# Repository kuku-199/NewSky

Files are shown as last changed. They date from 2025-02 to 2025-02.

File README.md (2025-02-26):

<<<<<<< HEAD
# NewSky📺
          
* [**中文版本**](/README_zh.md)

## Overview📖

=======
<h1 align="center">NewSky</h1>

           
* [**中文版本**](/README_zh.md)

## Overview📖
**Let beginners start making their own aircraft from scratch✈️**<br>
Projects that you can personally create:flight control ，racks (At present, we are not considering the production of ESC (the cost is too high))

**Supports multiple firmware options💿**<br>
NewSky Currently possessingPX4 Betaflight Inav Ardupolit firmware 

**Having different flight control models⚙️**<br>
NewSky use STM32 series as the main controller

## ⚠️⚠️⚠️ Commercial use without permission is strictly prohibited❗❗❗

### 📊Project Status 

|Complete|Making|Not started|
|-|-|-|
|✔|🛠️|❌|

## ⚙️Hardware<br>
### Flight controller
- ***NewSkyF7-Air*** ✔<br>

|Top|Bottom|
|:--:|:--:|
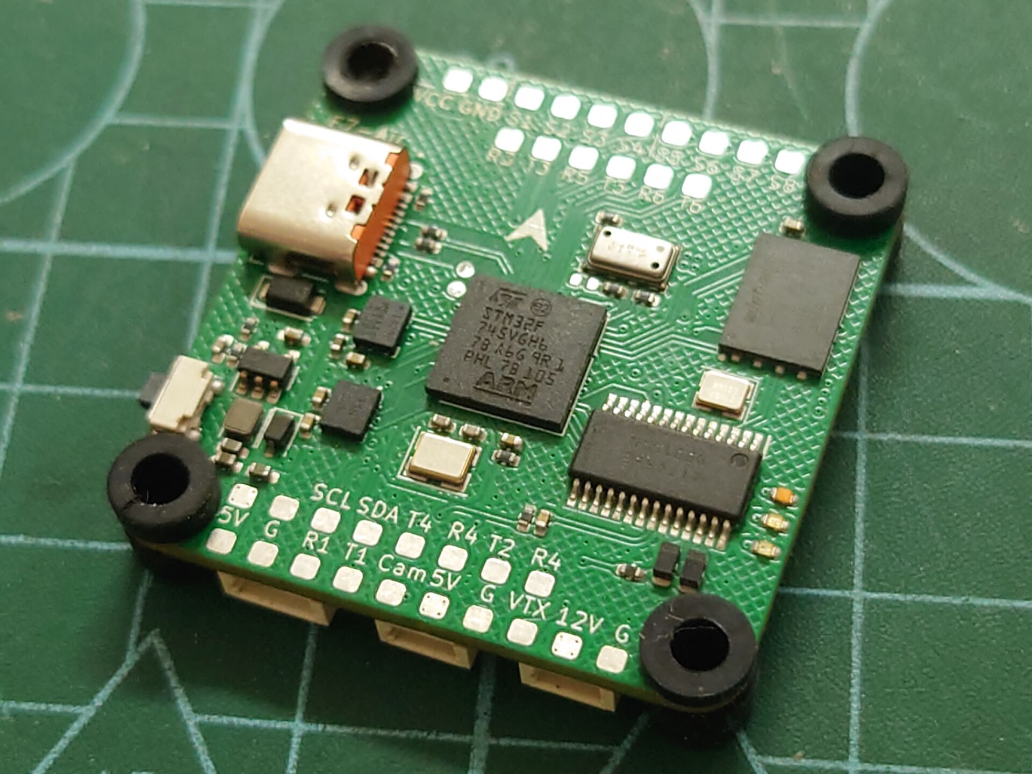
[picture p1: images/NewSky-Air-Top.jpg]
"up"
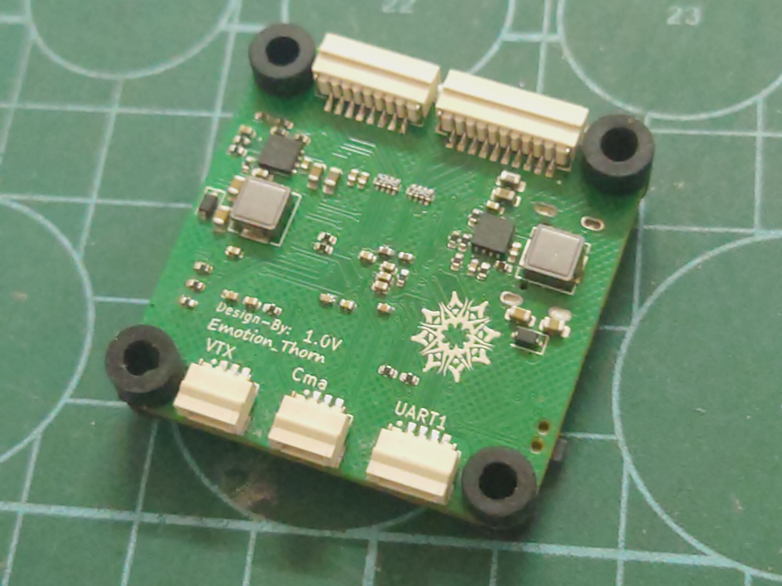
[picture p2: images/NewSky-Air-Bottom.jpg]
"down"
|||

- STM32F745VG(Cortex-M7)
- Have three BEC (Max input 36V)
    - 12V 3A
    - 5V 3A 
    - 3V3 2A
- Have two IMU
    - BMI270
    - IMC4288P
- On-board barometer(MS5611)
- On-board FLASH(W25Q256/W25N01G)
- On-board OSD(AT7456)
> In addition to the provided pad, which can be soldered, the board can use JST-SH

>Due to the lack of DMA channels in S5 S6, it seems that X8 mode (8 motors) cannot be activated on Betaflight at present

> The PCB engineering files have been open-source

- ***H7-Pro*** 🛠️

## ....

## 💿Firmware<br>
- Betaflight
    - NewSkyF7-Air (4.4.4-Beta)
- Ardupolit🛠️
- Inav🛠️
- PX4🛠️

## 🌐Wireless connection ground station 🛠️<br>
>>>>>>> c5ff180fc82f0e98c3e5e9217bb21fad2d1e034f

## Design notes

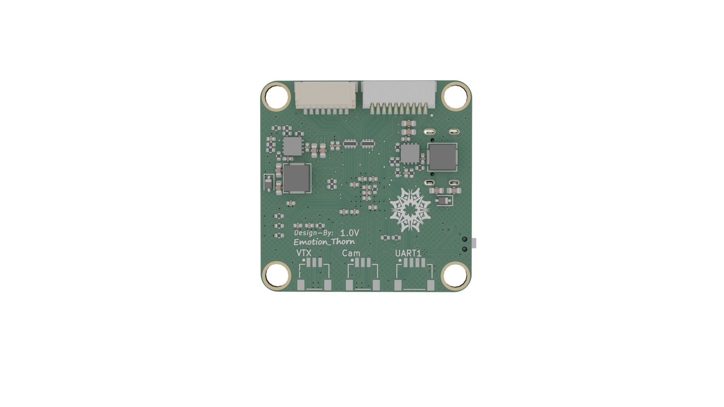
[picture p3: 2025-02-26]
images/NewSky-Air-Bottom1.png

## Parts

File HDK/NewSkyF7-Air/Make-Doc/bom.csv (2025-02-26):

Designator | Footprint | Quantity | Value | LCSC Part #
C1, C2, C3, C4 | 0603 | 4 | 10uF
C10, C11, C22, C24, C25, C27, C29, C30, C31, C32, C33, C36, C37, C38, C40, C41, C42, C44, C46, C5, C6, C8, C9 | 0402 | 23 | 100nF
C12 | 0402 | 1 | 6.8pF
C13, C16, C19 | 0402 | 3 | 10uF
C14, C15, C17, C18 | 0603 | 4 | 22uF
C20, C21 | 0402 | 2 | 15pF
C23, C7 | 0402 | 2 | 4.7uF
C26, C28, C45 | 0402 | 3 | 2.2uF
C34, C35 | 0603 | 2 | 47uF
C43 | 0402 | 1 | 10nF
D1, D2, D3 | D_SOD-323 | 3 | LESD3Z5.0CMT1G
D4 | 0402 | 1 | Red
D5 | 0402 | 1 | Yellow
D6 | 0402 | 1 | Blue
D7 | D_SOD-123F | 1 | K24
IC1, IC2 | MP9943GQZ | 2 | MP9943GQ-Z
IC3 | IIM42352 | 1 | ICM-42688-P
IC4 | SON127P800X600X80-9N-D | 1 | W25Q256JVEIQ
J1 | JST_SM04B-SRSS-TB(LF)(SN) | 1 | SBUS
J10, J11, J12, J13, J14, J15, J16, J17, J18, J19, J20, J21, J22, J23, J24, J25, J26, J27, J28, J29, J30, J31, J32, J33, J34, J37, J38, J39, J40, J5, J6, J7, J8, J9 | Test | 34 | Conn_01x01_Socket
J2 | JST_SM03B-SRSS-TB(LF)(SN) | 1 | VTX
J3 | JST_SM03B-SRSS-TB(LF)(SN) | 1 | Camera
J35 | NewSkyF7 | 1 | ~
J36 | SM10B-SRSS-TB | 1 | Conn_01x10_Socket
J4 | SH1.0mm_8P | 1 | Input
J41, J42 | TestPoint_Pad_D1.0mm | 2 | Conn_01x01_Socket
L1 | L_Murata_DFE201610P | 1 | 2.2uH
L2, L3 | L_Sunlord_MWSA0402S | 2 | L
R1, R2, R3, R33, R4, R6 | 0402 | 6 | 100K
R10, R24, R25, R8 | 0402 | 4 | 22R
R11 | 0402 | 1 | 3K
R12 | 0402 | 1 | 7.68K
R13, R14 | 0402 | 2 | 41.2K
R15, R18, R19, R29, R30, R34, R35 | 0402 | 7 | 10K
R16, R20, R21, R26 | 0402 | 4 | 1K
R17 | 0402 | 1 | 3.3K
R22, R23 | 0402 | 2 | 5.1K
R27, R28 | 0402 | 2 | 75R
R31, R32 | 0402 | 2 | [N/S]
R5 | 0402 | 1 | 442K
R7, R9 | 0402 | 2 | 51K
RN1, RN2 | R_Array_Concave_4x0402 | 2 | 22R
SW1 | 2x4_side | 1 | BOOT0
U1 | SOT-23-5 | 1 | TLV62569DBV
U2 | TFBGA-100_8x8mm_Layout10x10_P0.8mm | 1 | STM32F745VGH6
U4 | Typc-C-16P | 1 | USB_C_16P
U5 | SOP65P640X120-29N | 1 | AT7456E
U6 | XDCR_BMI270 | 1 | BMI270
U8 | LGA-8_3x5mm_P1.25mm | 1 | MS5611-01BA
Y1 | Crystal_SMD_3225-4Pin_3.2x2.5mm | 1 | 25M
Y2 | Crystal_SMD_2520-4Pin_2.5x2.0mm | 1 | 27M

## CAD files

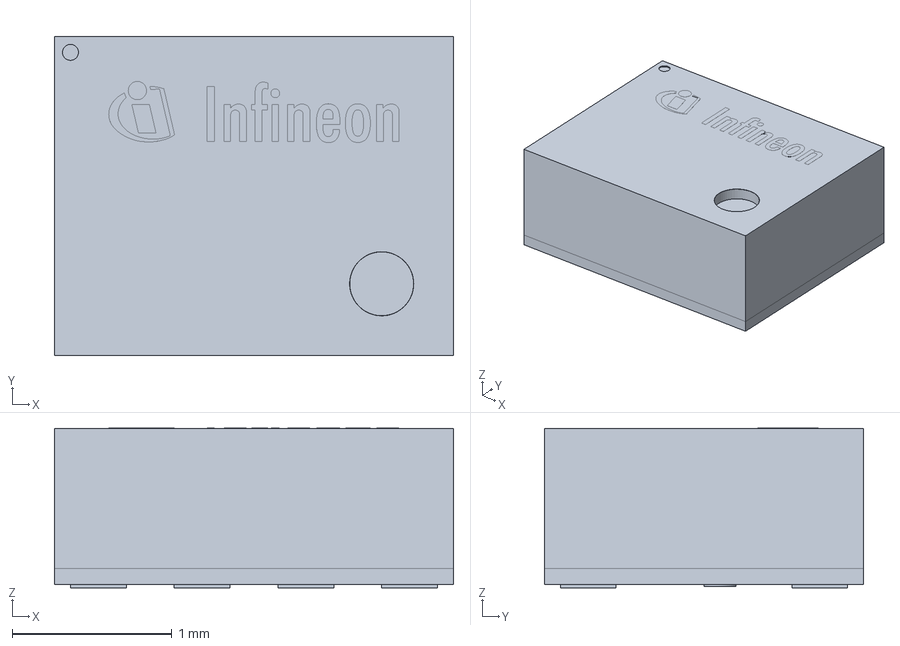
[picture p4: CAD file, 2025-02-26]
HDK/Design-file/3D/DPS310XTSA1.stp
2.50 x 2.00 x 1.00 mm
CADSOFTTOOLS 2.1
CADSOFTTOOLS 2.2
CADSOFTTOOLS 2.3
CADSOFTTOOLS 2.4
CADSOFTTOOLS 2.5
CADSOFTTOOLS 2.6
CADSOFTTOOLS 2.7
CADSOFTTOOLS 2.8
CADSOFTTOOLS 2.9
CADSOFTTOOLS 2.10
CADSOFTTOOLS 2.11
CADSOFTTOOLS 2.12
CADSOFTTOOLS 2.13
CADSOFTTOOLS 2.14
CADSOFTTOOLS 2.15
CADSOFTTOOLS 2.16
CADSOFTTOOLS 2.17
CADSOFTTOOLS 2.18
CADSOFTTOOLS 2.19
CADSOFTTOOLS 2.20
CADSOFTTOOLS 2.21
CADSOFTTOOLS 2.22
CADSOFTTOOLS 2.23
CADSOFTTOOLS 2.24
CADSOFTTOOLS 2.25
CADSOFTTOOLS 2.26
CADSOFTTOOLS 2.27
CADSOFTTOOLS 2.28
CADSOFTTOOLS 2.29
CADSOFTTOOLS 2.30
CADSOFTTOOLS 2.31
CADSOFTTOOLS 2.32
CADSOFTTOOLS 2.33
CADSOFTTOOLS 2.34
CADSOFTTOOLS 2.35
CADSOFTTOOLS 2.36
CADSOFTTOOLS 2.37
CADSOFTTOOLS 2.38
CADSOFTTOOLS 2.39
CADSOFTTOOLS 2.40
CADSOFTTOOLS 2.41
CADSOFTTOOLS 2.42
CADSOFTTOOLS 2.43
CADSOFTTOOLS 2.44
CADSOFTTOOLS 2.45
CADSOFTTOOLS 2.46
CADSOFTTOOLS 2.47
CADSOFTTOOLS 2.48
CADSOFTTOOLS 2.49
CADSOFTTOOLS 2.50
CADSOFTTOOLS 2.51
CADSOFTTOOLS 2.52
CADSOFTTOOLS 2.53
CADSOFTTOOLS 2.54
CADSOFTTOOLS 2.55
CADSOFTTOOLS 2.56
CADSOFTTOOLS 2.57
CADSOFTTOOLS 2.58
CADSOFTTOOLS 2.59
CADSOFTTOOLS 2.60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

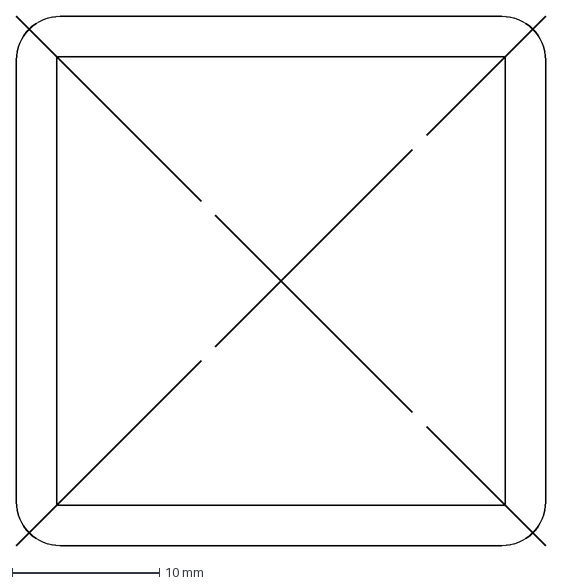
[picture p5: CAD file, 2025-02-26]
HDK/NewSkyF7-Air/Outline.dxf
36.0 x 36.0 mm

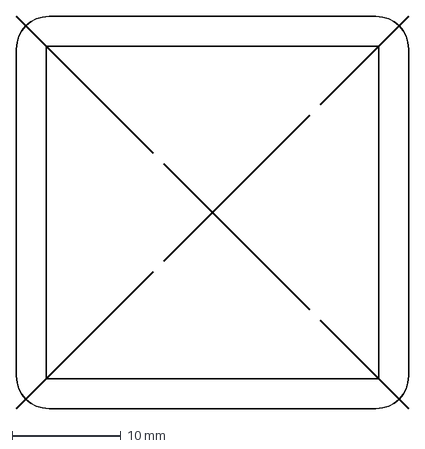
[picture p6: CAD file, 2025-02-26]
HDK/NewSkyH7-Air/Outline.dxf
36.0 x 36.0 mm

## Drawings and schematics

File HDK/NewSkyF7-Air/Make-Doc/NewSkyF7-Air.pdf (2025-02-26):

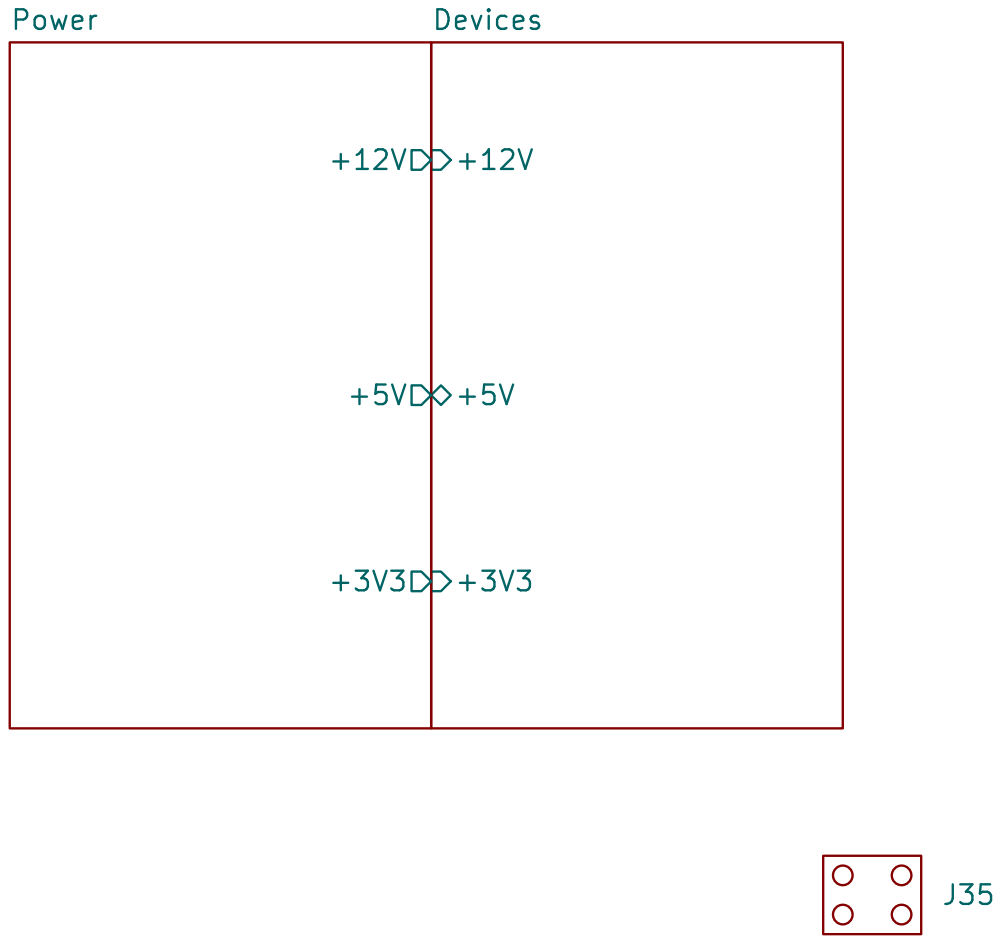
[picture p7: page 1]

Id: 1/7 Title: NewSkyF7-Air File: / Sheet: /

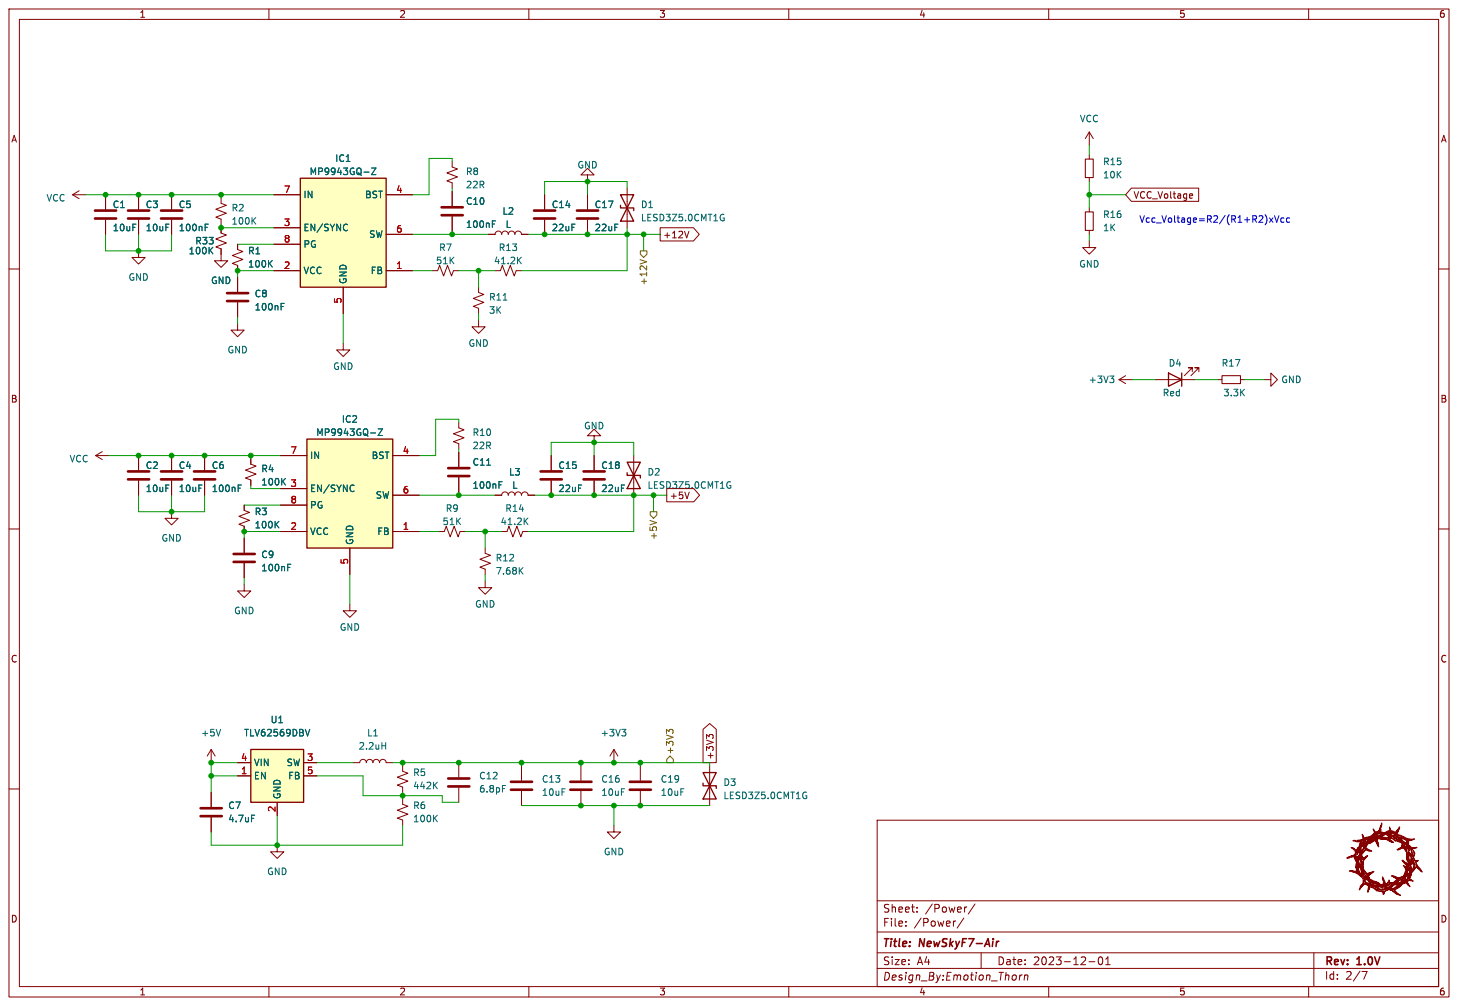
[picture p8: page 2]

Id: 2/7 Title: NewSkyF7-Air File: /Power/ Sheet: /Power/ +3V3

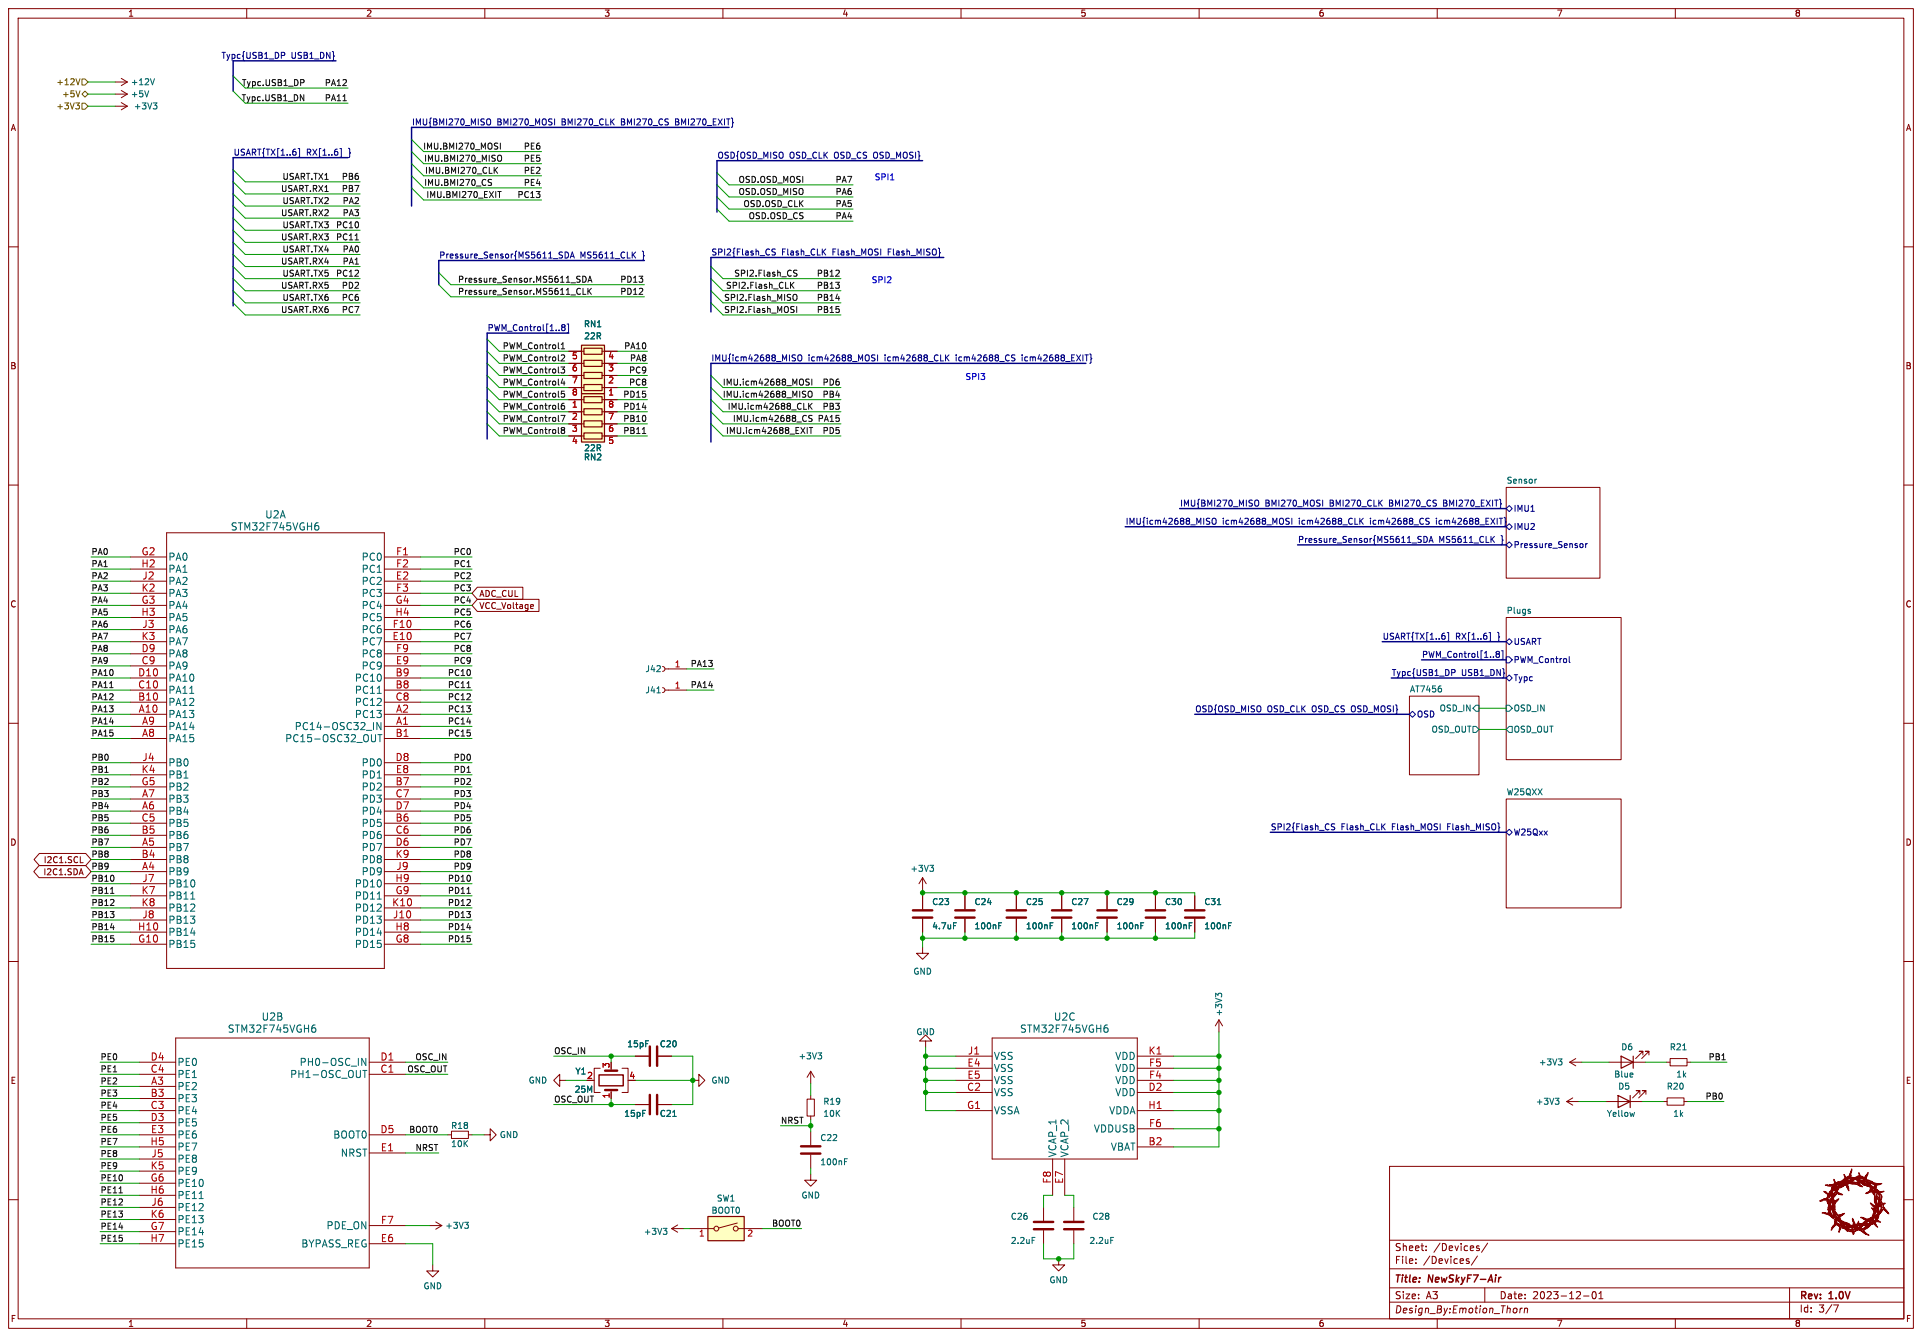
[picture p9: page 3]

Id: 3/7 Title: NewSkyF7-Air File: /Devices/ Sheet: /Devices/

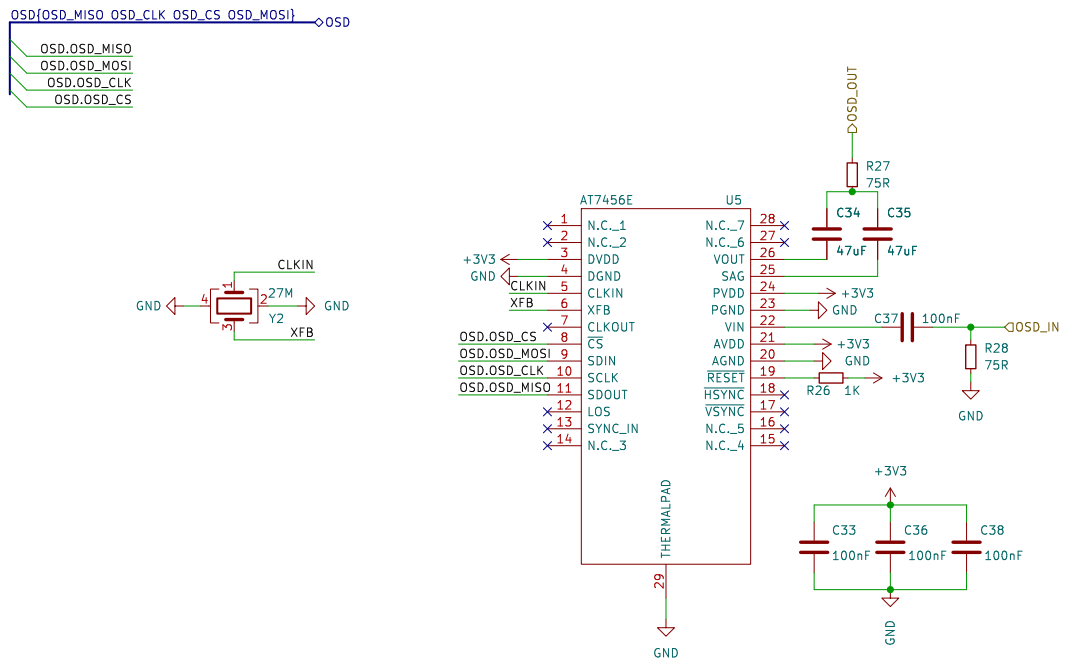
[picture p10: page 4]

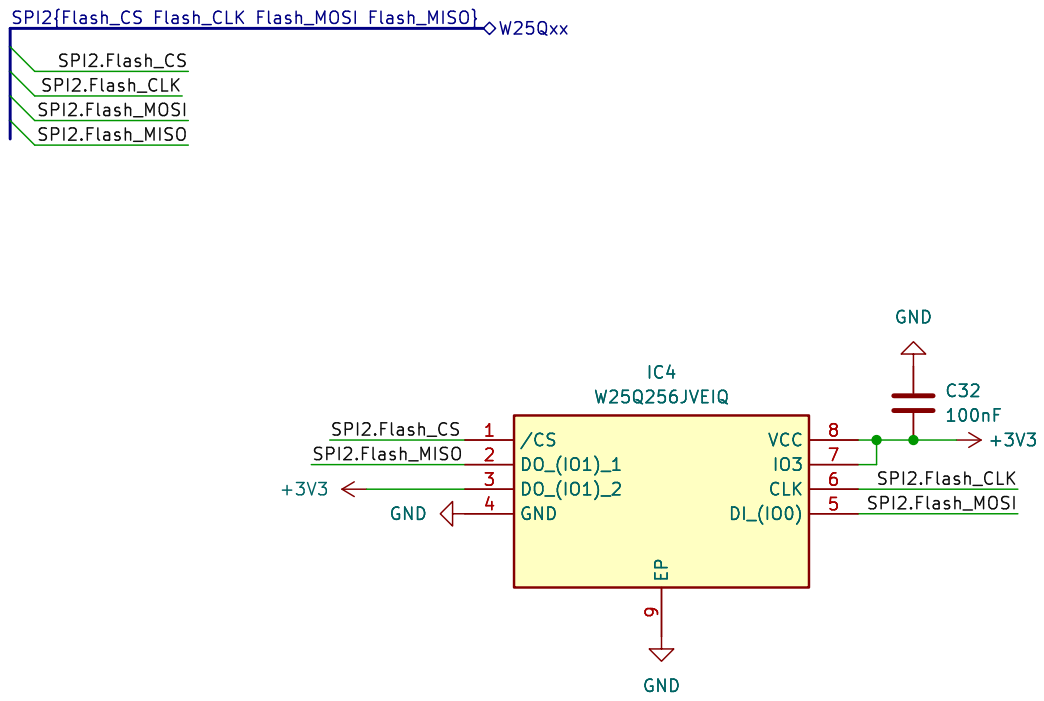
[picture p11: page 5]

Id: 5/7 Title: NewSkyF7-Air File: /Devices/W25QXX/ Sheet: /Devices/W25QXX/

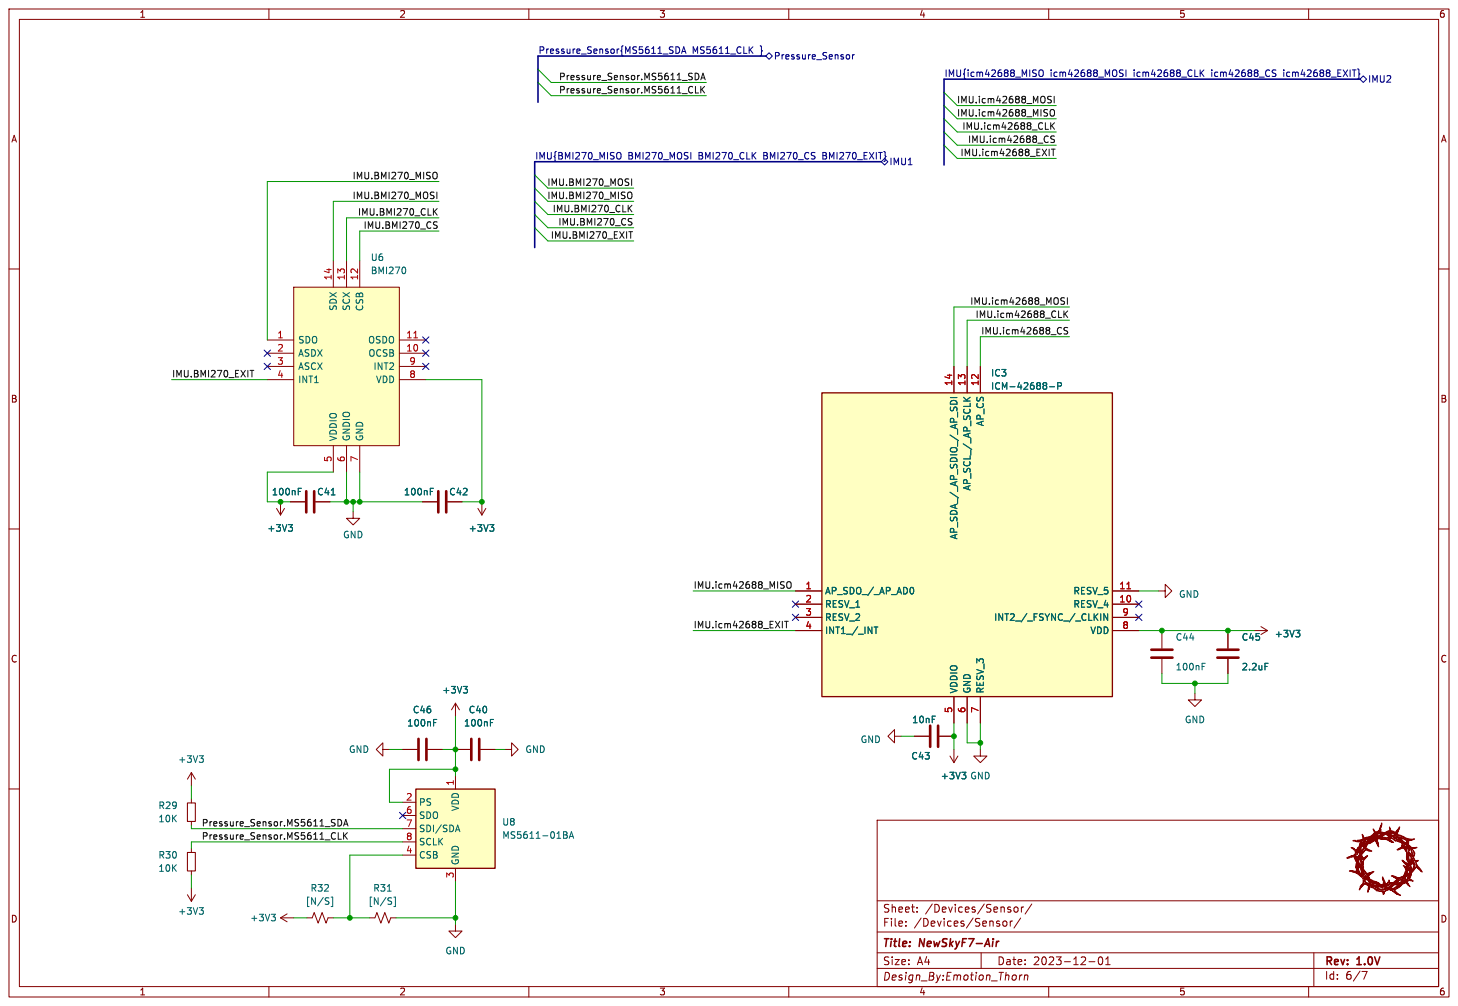
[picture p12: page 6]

3 CSB 4 SDO 6 SDI/SDA 7 SCLK 8 U8 MS5611-01BA GND

Id: 6/7 Title: NewSkyF7-Air File: /Devices/Sensor/ Sheet: /Devices/Sensor/ R32

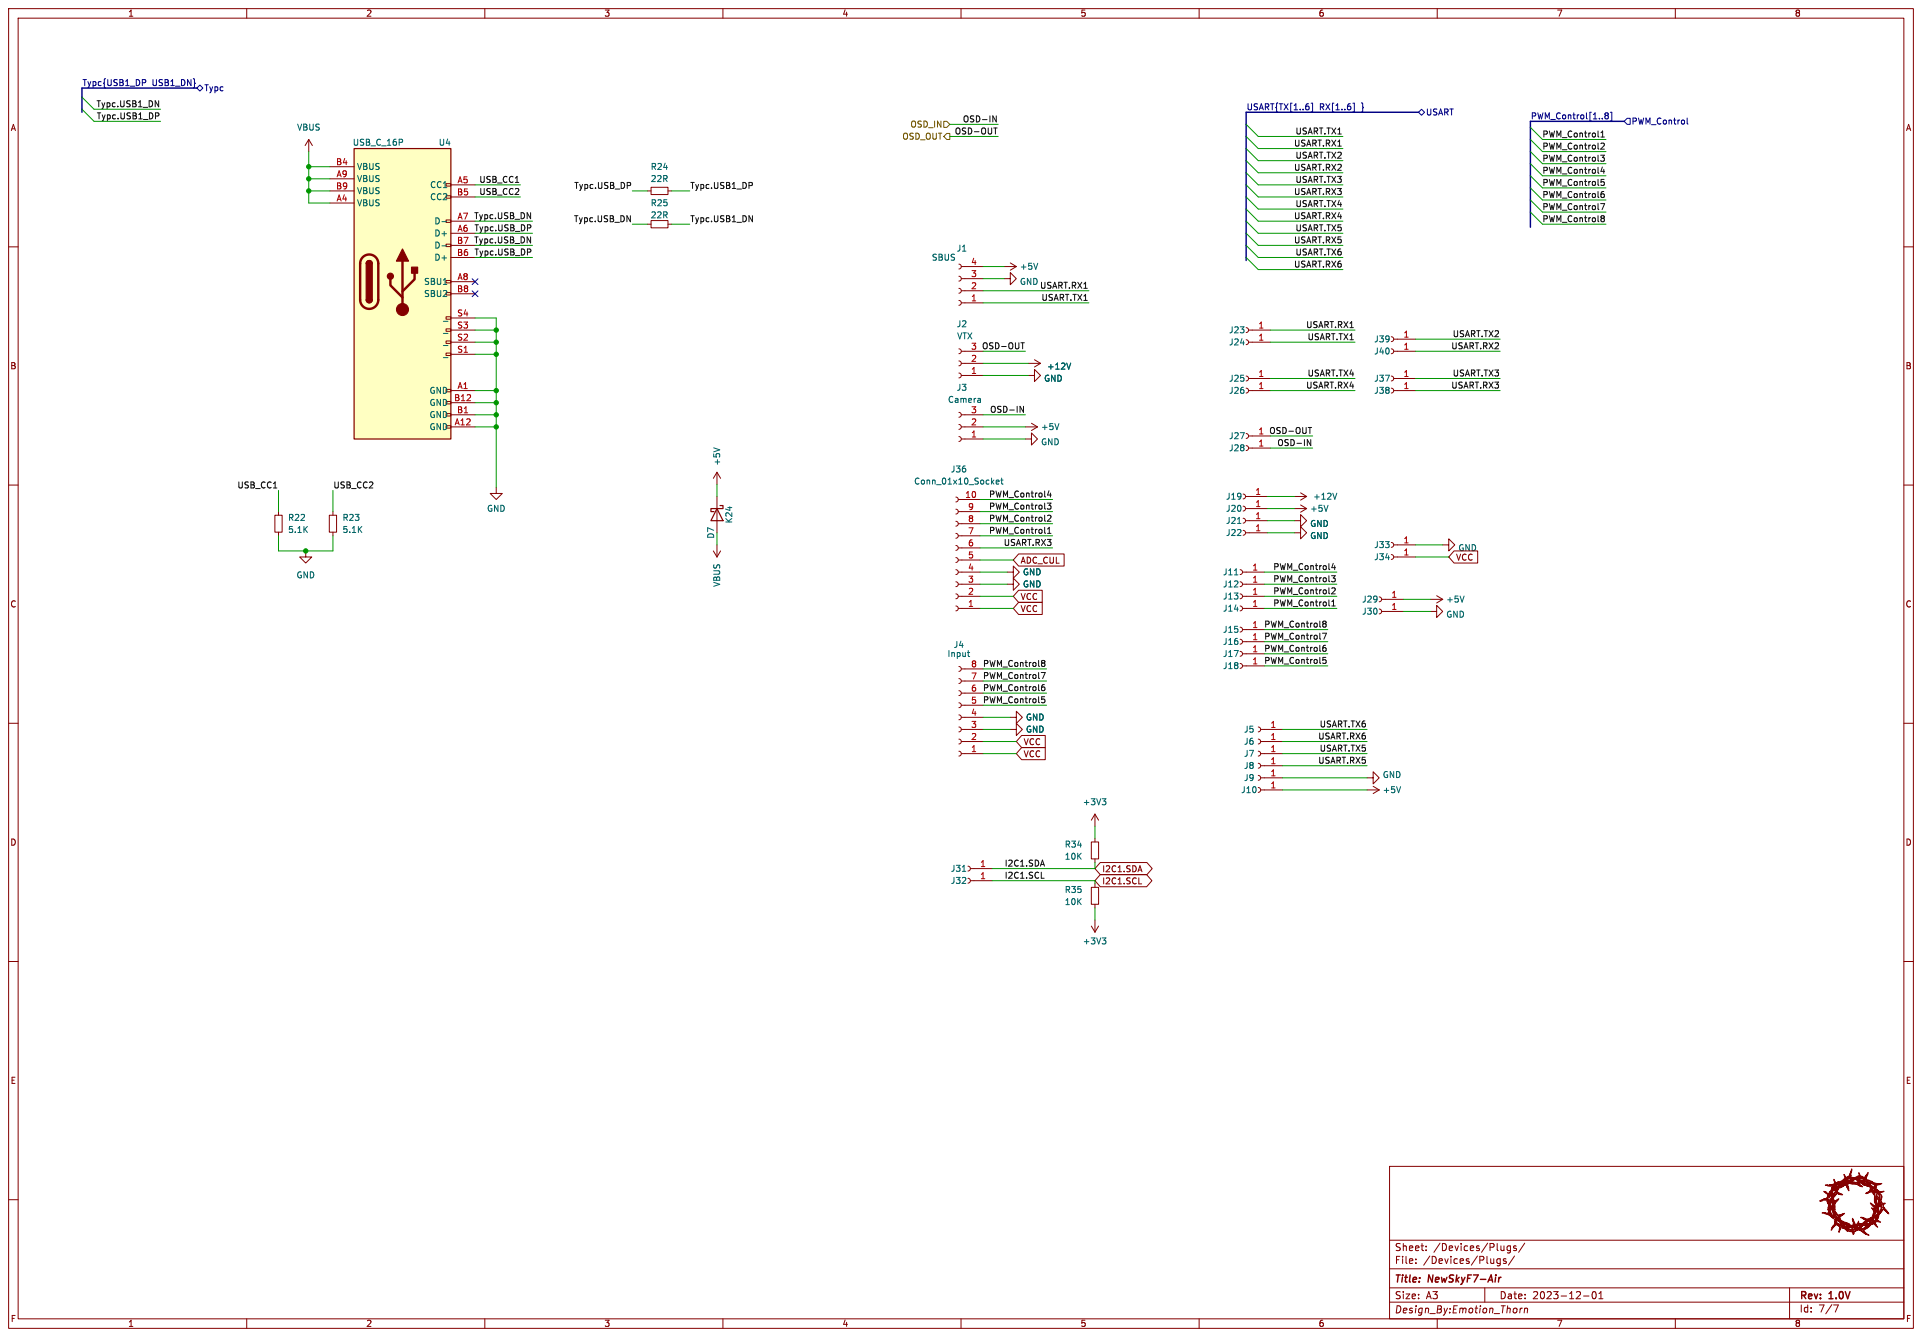
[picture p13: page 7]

Id: 7/7 Title: NewSkyF7-Air File: /Devices/Plugs/ Sheet: /Devices/Plugs/

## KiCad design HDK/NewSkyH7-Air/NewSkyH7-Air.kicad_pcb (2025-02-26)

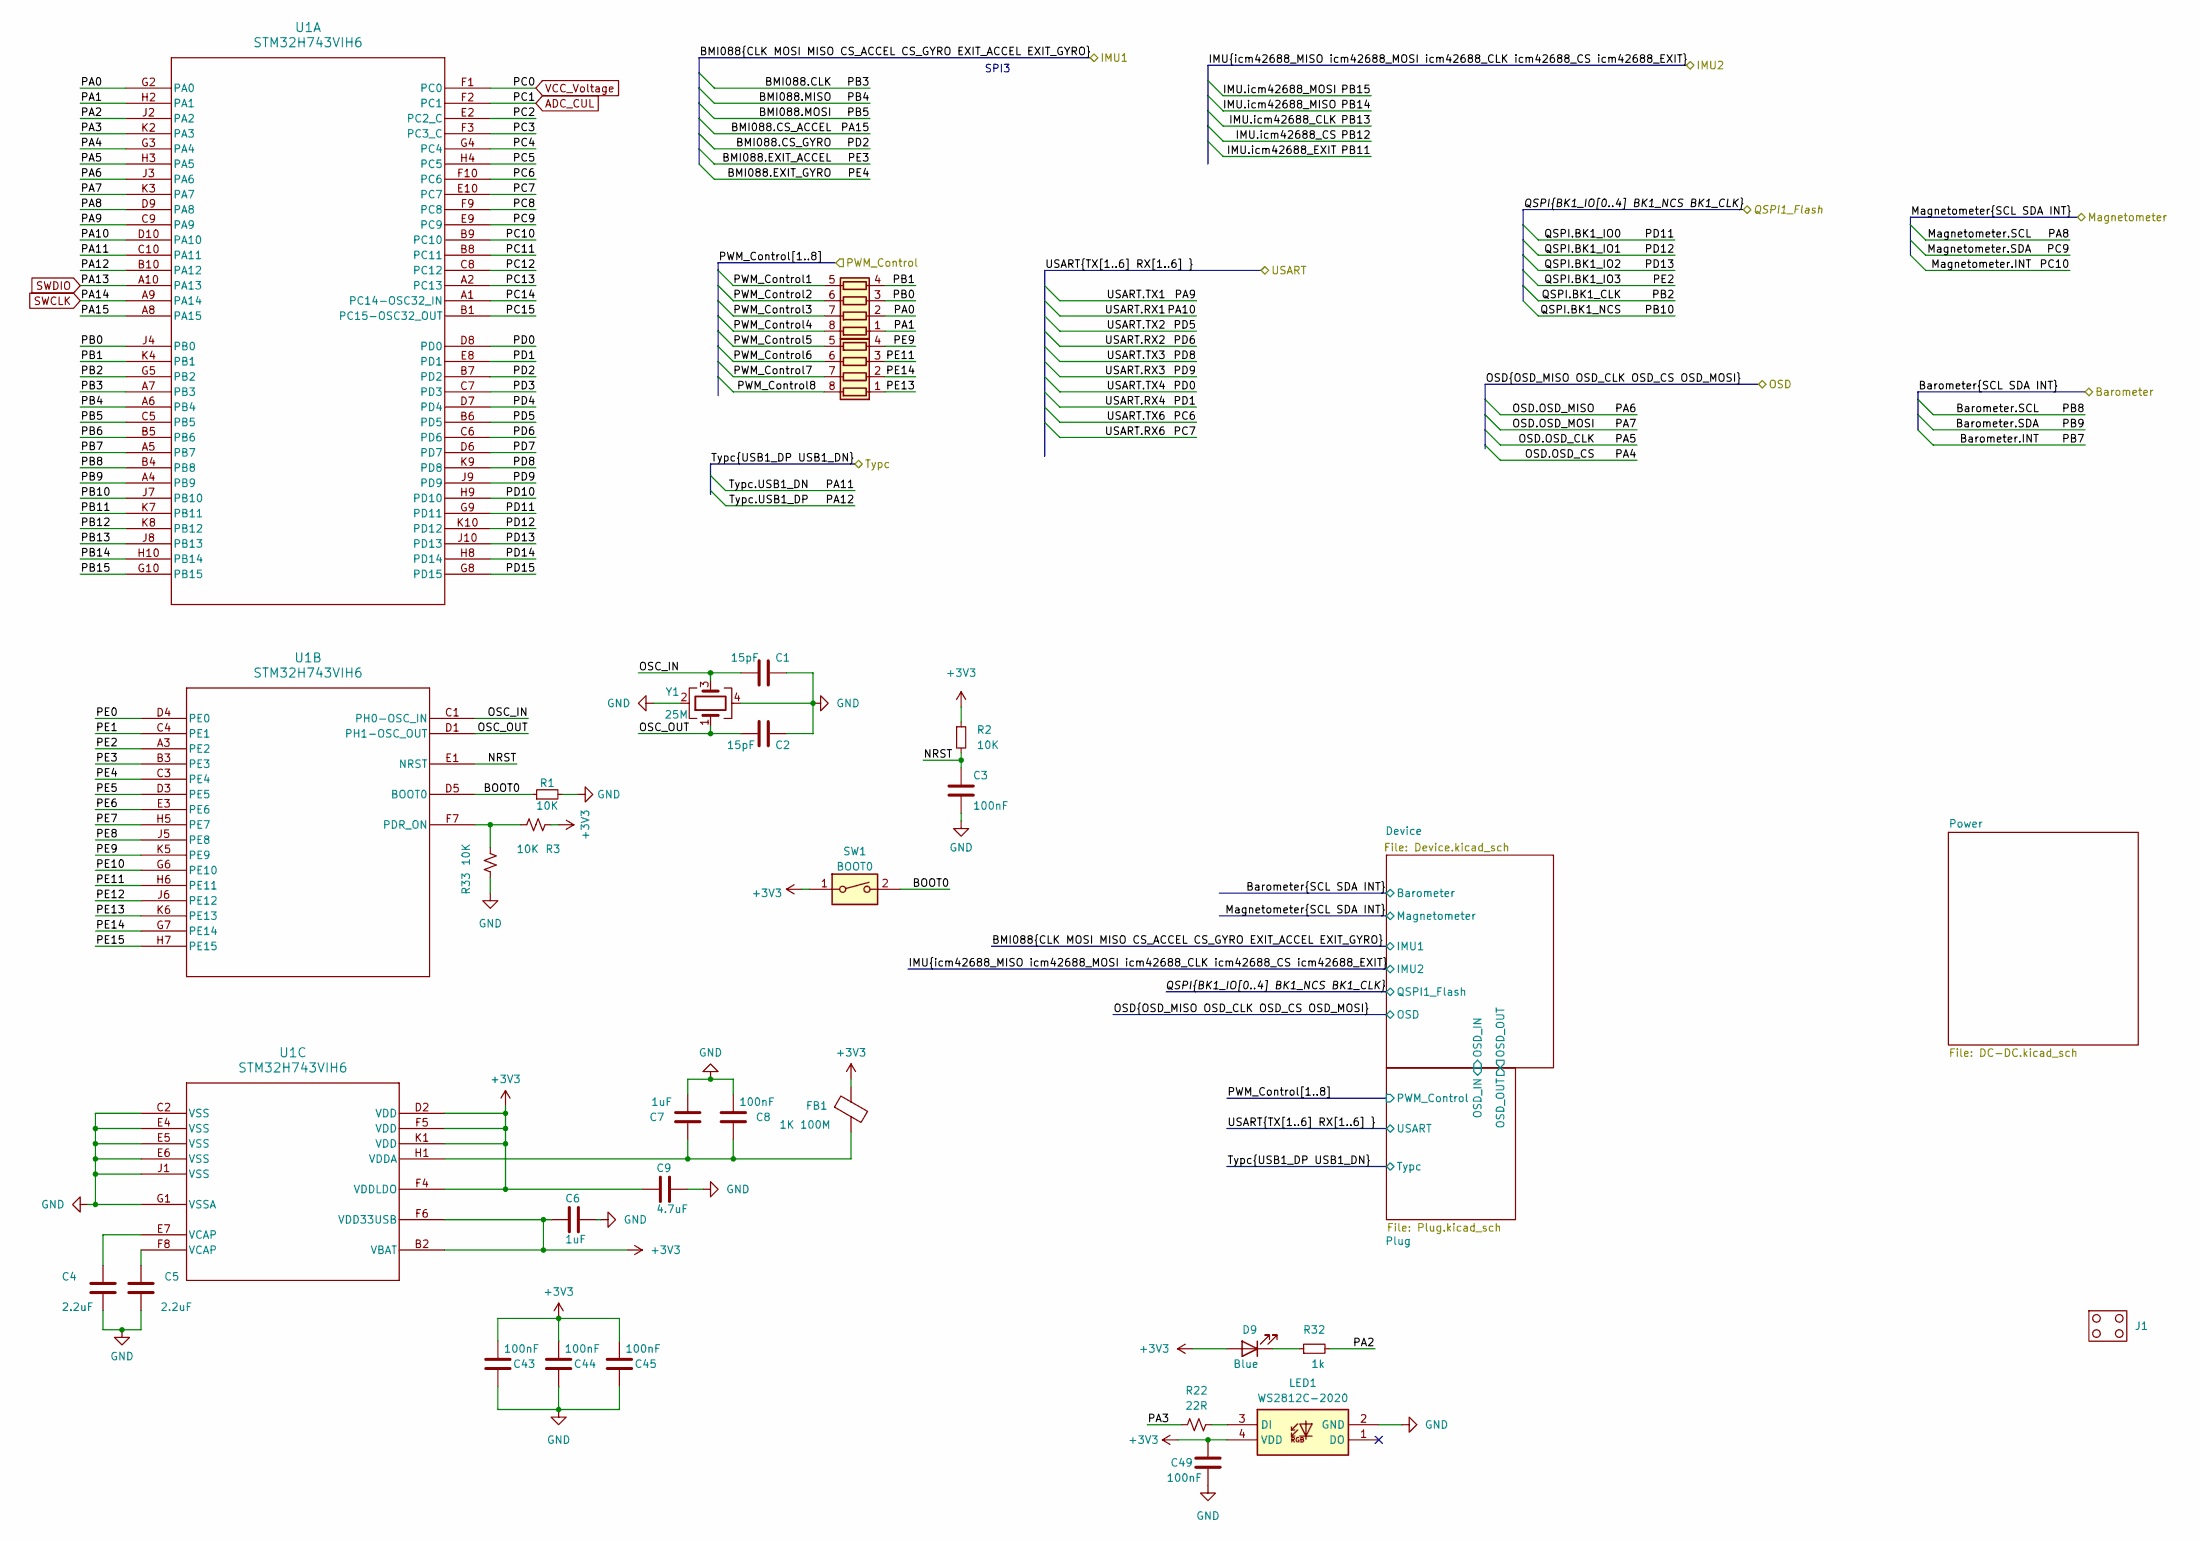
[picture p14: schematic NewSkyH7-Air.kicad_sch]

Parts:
C1, C2: 15pF; C_0402_1005Metric
C3, C8, C43, C44, C45, C49: 100nF; C_0402_1005Metric
C4, C5: 2.2uF; C_0402_1005Metric
C6, C7: 1uF; C_0402_1005Metric
C9: 4.7uF; C_0402_1005Metric
D9: Blue; LED_0402_1005Metric
FB1: 1K 100M; L_0402_1005Metric
J1: NewSkyH7-Outline
LED1: WS2812C-2020; WS2812C2020; Manufacturer_Part_Number WS2812C-2020
R1, R2, R3, R33: 10K; R_0402_1005Metric
R22: 22R; R_0402_1005Metric
R32: 1k; R_0402_1005Metric
RN1, RN2: 22R; R_Array_Concave_4x0402
SW1: BOOT0; 2x4_side
U1: STM32H743VIH6; TFBGA-100_8x8mm_Layout10x10_P0.8mm
Y1: 25M; Crystal_SMD_2016-4Pin_2.0x1.6mm

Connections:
+3V3: C6.2, C9.2, C43.2, C44.2, C45.2, C49.1, D9.2 (A), FB1.1, LED1.4 (VDD), R2.1, R3.1, SW1.1, U1.B2 (VBAT), U1.D2 (VDD), U1.F4 (VDDLDO), U1.F5 (VDD), U1.F6 (VDD33USB), U1.K1 (VDD); also elsewhere on the board
/BMI088.CLK: U1.A7 (PB3); also elsewhere on the board
/BMI088.CS_ACCEL: U1.A8 (PA15); also elsewhere on the board
/BMI088.CS_GYRO: U1.B7 (PD2); also elsewhere on the board
/BMI088.EXIT_ACCEL: U1.B3 (PE3); also elsewhere on the board
/BMI088.EXIT_GYRO: U1.C3 (PE4); also elsewhere on the board
/BMI088.MISO: U1.A6 (PB4); also elsewhere on the board
/BMI088.MOSI: U1.C5 (PB5); also elsewhere on the board
/BOOT0: R1.1, SW1.2, U1.D5 (BOOT0)
/Barometer.INT: U1.A5 (PB7); also elsewhere on the board
/Barometer.SCL: U1.B4 (PB8); also elsewhere on the board
/Barometer.SDA: U1.A4 (PB9); also elsewhere on the board
/IMU.icm42688_CLK: U1.J8 (PB13); also elsewhere on the board
/IMU.icm42688_CS: U1.K8 (PB12); also elsewhere on the board
/IMU.icm42688_EXIT: U1.K7 (PB11); also elsewhere on the board
/IMU.icm42688_MISO: U1.H10 (PB14); also elsewhere on the board
/IMU.icm42688_MOSI: U1.G10 (PB15); also elsewhere on the board
/Magnetometer.INT: U1.B9 (PC10); also elsewhere on the board
/Magnetometer.SCL: U1.D9 (PA8); also elsewhere on the board
/Magnetometer.SDA: U1.E9 (PC9); also elsewhere on the board
/NRST: C3.1, R2.2, U1.E1 (NRST)
/OSC_IN: C1.1, U1.C1 (PH0-OSC_IN), Y1.3
/OSC_OUT: C2.1, U1.D1 (PH1-OSC_OUT), Y1.1
/OSD.OSD_CLK: U1.H3 (PA5); also elsewhere on the board
/OSD.OSD_CS: U1.G3 (PA4); also elsewhere on the board
/OSD.OSD_MISO: U1.J3 (PA6); also elsewhere on the board
/OSD.OSD_MOSI: U1.K3 (PA7); also elsewhere on the board
/PA0: RN1.2 (R2.1), U1.G2 (PA0)
/PA1: RN1.1 (R1.1), U1.H2 (PA1)
/PA2: R32.2, U1.J2 (PA2)
/PA3: R22.1, U1.K2 (PA3)
/PB0: RN1.3 (R3.1), U1.J4 (PB0)
/PB1: RN1.4 (R4.1), U1.K4 (PB1)
/PB6: U1.B5 (PB6)
/PC2: U1.E2 (PC2_C)
/PC3: U1.F3 (PC3_C)
/PC4: U1.G4 (PC4)
/PC5: U1.H4 (PC5)
/PC8: U1.F9 (PC8)
/PC11: U1.B8 (PC11)
/PC12: U1.C8 (PC12)
/PC13: U1.A2 (PC13)
/PC14: U1.A1 (PC14-OSC32_IN)
/PC15: U1.B1 (PC15-OSC32_OUT)
/PD3: U1.C7 (PD3)
/PD4: U1.D7 (PD4)
/PD7: U1.D6 (PD7)
/PD10: U1.H9 (PD10)
/PD14: U1.H8 (PD14)
/PD15: U1.G8 (PD15)
/PE0: U1.D4 (PE0)
/PE1: U1.C4 (PE1)
/PE5: U1.D3 (PE5)
/PE6: U1.E3 (PE6)
/PE7: U1.H5 (PE7)
/PE8: U1.J5 (PE8)
/PE9: RN2.4 (R4.1), U1.K5 (PE9)
/PE10: U1.G6 (PE10)
/PE11: RN2.3 (R3.1), U1.H6 (PE11)
/PE12: U1.J6 (PE12)
/PE13: RN2.1 (R1.1), U1.K6 (PE13)
/PE14: RN2.2 (R2.1), U1.G7 (PE14)
/PE15: U1.H7 (PE15)
/PWM_Control1: RN1.5 (R4.2); also elsewhere on the board
/PWM_Control2: RN1.6 (R3.2); also elsewhere on the board
/PWM_Control3: RN1.7 (R2.2); also elsewhere on the board
/PWM_Control4: RN1.8 (R1.2); also elsewhere on the board
/PWM_Control5: RN2.5 (R4.2); also elsewhere on the board
/PWM_Control6: RN2.6 (R3.2); also elsewhere on the board
/PWM_Control7: RN2.7 (R2.2); also elsewhere on the board
/PWM_Control8: RN2.8 (R1.2); also elsewhere on the board
/QSPI.BK1_CLK: U1.G5 (PB2); also elsewhere on the board
/QSPI.BK1_IO0: U1.G9 (PD11); also elsewhere on the board
/QSPI.BK1_IO1: U1.K10 (PD12); also elsewhere on the board
/QSPI.BK1_IO2: U1.J10 (PD13); also elsewhere on the board
/QSPI.BK1_IO3: U1.A3 (PE2); also elsewhere on the board
/QSPI.BK1_NCS: U1.J7 (PB10); also elsewhere on the board
/Typc.USB1_DN: U1.C10 (PA11); also elsewhere on the board
/Typc.USB1_DP: U1.B10 (PA12); also elsewhere on the board
/USART.RX1: U1.D10 (PA10); also elsewhere on the board
/USART.RX2: U1.C6 (PD6); also elsewhere on the board
/USART.RX3: U1.J9 (PD9); also elsewhere on the board
/USART.RX4: U1.E8 (PD1); also elsewhere on the board
/USART.RX6: U1.E10 (PC7); also elsewhere on the board
/USART.TX1: U1.C9 (PA9); also elsewhere on the board
/USART.TX2: U1.B6 (PD5); also elsewhere on the board
/USART.TX3: U1.K9 (PD8); also elsewhere on the board
/USART.TX4: U1.D8 (PD0); also elsewhere on the board
/USART.TX6: U1.F10 (PC6); also elsewhere on the board
ADC_CUL: U1.F2 (PC1); also elsewhere on the board
GND: C1.2, C2.2, C3.2, C4.2, C5.2, C6.1, C7.2, C8.2, C9.1, C43.1, C44.1, C45.1, C49.2, LED1.2 (GND), R1.2, R33.1, U1.C2 (VSS), U1.E4 (VSS), U1.E5 (VSS), U1.E6 (VSS), U1.G1 (VSSA), U1.J1 (VSS), Y1.2, Y1.4; also elsewhere on the board
unnamed: C4.1, U1.E7 (VCAP)
unnamed: C5.1, U1.F8 (VCAP)
unnamed: D9.1 (K), R32.1
unnamed: LED1.3 (DI), R22.2
unnamed: R3.2, R33.2, U1.F7 (PDR_ON)
unnamed: C7.1, C8.1, FB1.2, U1.H1 (VDDA)
SWCLK: U1.A9 (PA14); also elsewhere on the board
SWDIO: U1.A10 (PA13); also elsewhere on the board
VCC_Voltage: U1.F1 (PC0); also elsewhere on the board

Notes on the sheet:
SPI3

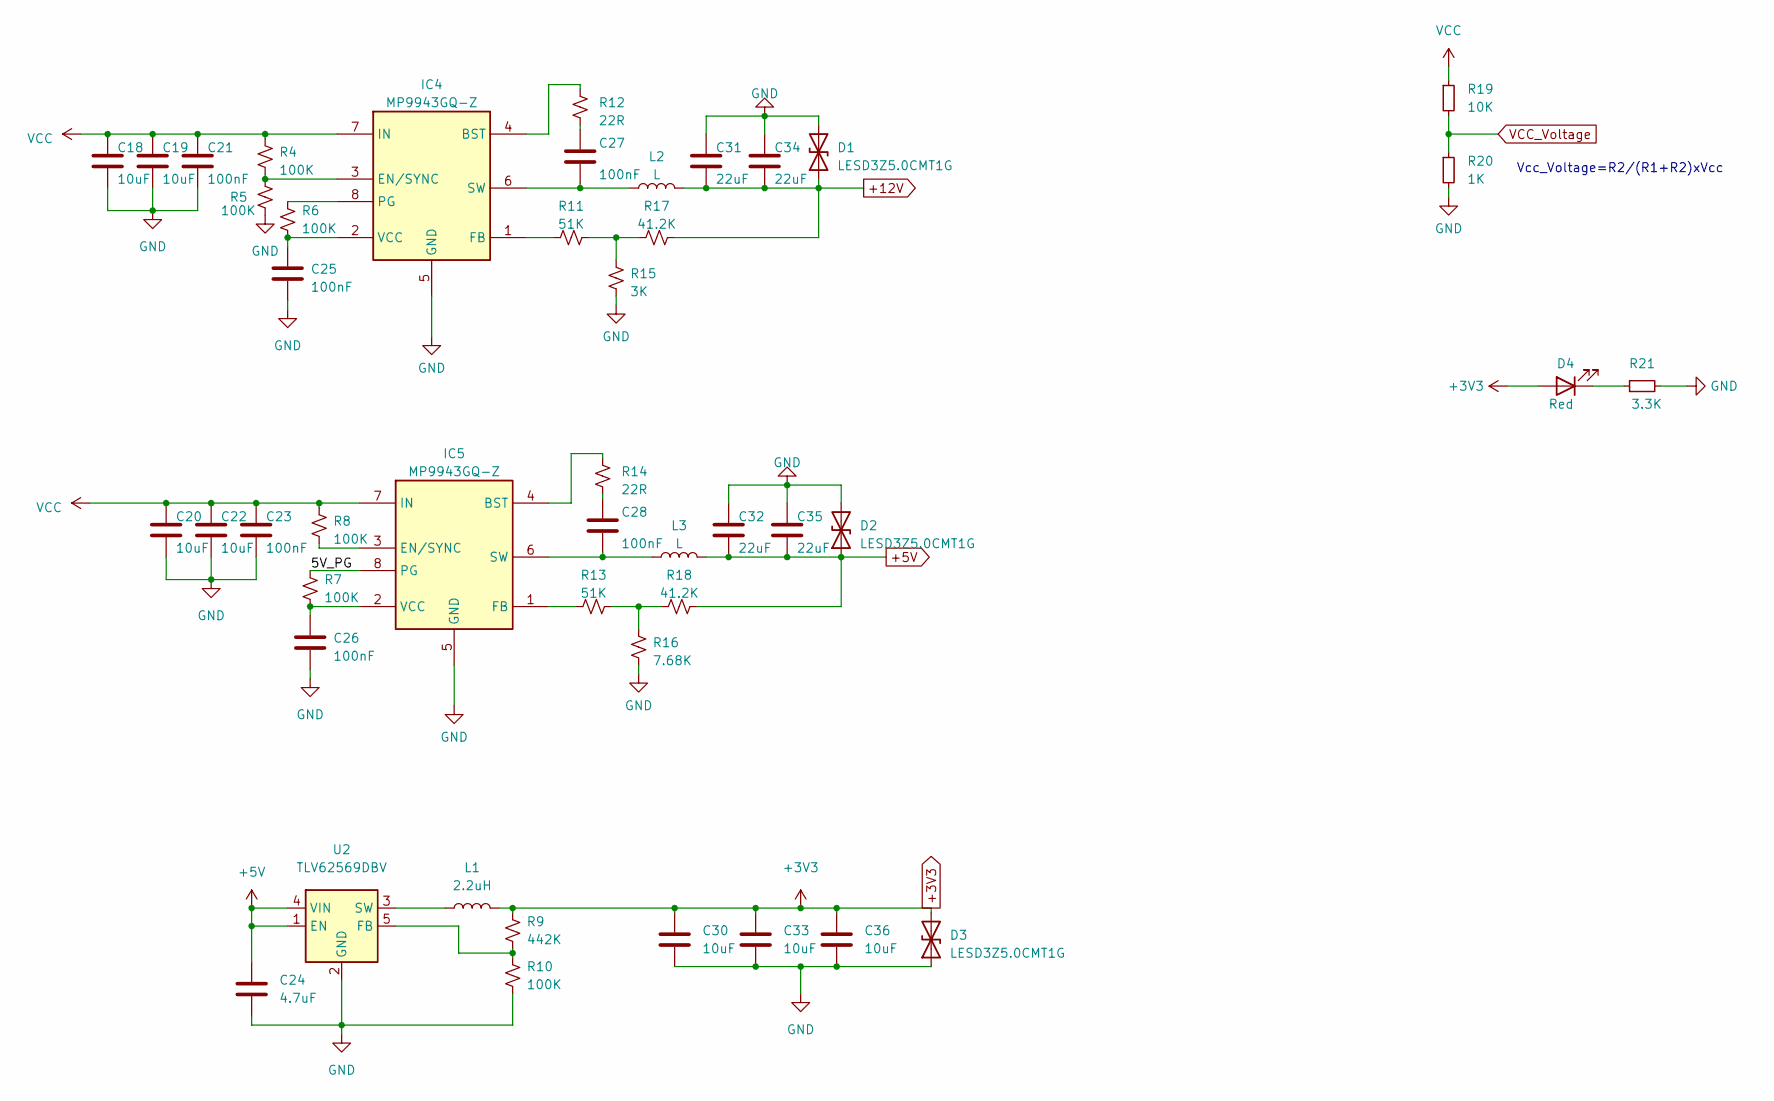
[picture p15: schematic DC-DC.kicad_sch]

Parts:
C18, C19, C20, C22: 10uF; C_0603_1608Metric
C21, C23, C25, C26: 100nF; C_0402_1005Metric
C24: 4.7uF; C_0402_1005Metric_Pad0.74x0.62mm_HandSolder
C27, C28: 100nF; C_0402_1005Metric_Pad0.74x0.62mm_HandSolder
C30, C33, C36: 10uF; C_0402_1005Metric_Pad0.74x0.62mm_HandSolder
C31, C32, C34, C35: 22uF; C_0805_2012Metric
D1, D2, D3: LESD3Z5.0CMT1G; D_SOD-323
D4: Red; LED_0402_1005Metric
IC4, IC5: MP9943GQ-Z; MP9943GQZ; Manufacturer_Part_Number MP9943GQ-Z; Mouser Part Number 946-MP9943GQ-Z
L1: 2.2uH; L_Murata_DFE201610P
L2, L3: L; L_Sunlord_MWSA0402S
R4, R5, R6, R7, R8, R10: 100K; R_0402_1005Metric
R9: 442K; R_0402_1005Metric
R11, R13: 51K; R_0402_1005Metric
R12, R14: 22R; R_0402_1005Metric
R15: 3K; R_0402_1005Metric
R16: 7.68K; R_0402_1005Metric
R17, R18: 41.2K; R_0402_1005Metric
R19: 10K; R_0402_1005Metric
R20: 1K; R_0402_1005Metric
R21: 3.3K; R_0402_1005Metric
U2: TLV62569DBV; SOT-23-5

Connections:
+3V3: C30.1, C33.1, C36.1, D3.2 (A2), D4.2 (A), L1.2, R9.1; also elsewhere on the board
+5V: C24.1, C32.2, C35.2, D2.1 (A1), L3.2, R18.2, U2.1 (EN), U2.4 (VIN); also elsewhere on the board
+12V: C31.2, C34.2, D1.1 (A1), L2.2, R17.2; also elsewhere on the board
/Power/5V_PG: IC5.8 (PG), R7.1
GND: C18.2, C19.2, C20.2, C21.2, C22.2, C23.2, C24.2, C25.2, C26.2, C30.2, C31.1, C32.1, C33.2, C34.1, C35.1, C36.2, D1.2 (A2), D2.2 (A2), D3.1 (A1), IC4.5 (GND), IC5.5 (GND), R5.2, R10.2, R15.2, R16.2, R20.2, R21.2, U2.2 (GND); also elsewhere on the board
unnamed: C27.1, R12.2
unnamed: C28.1, R14.2
unnamed: D4.1 (K), R21.1
unnamed: IC4.4 (BST), R12.1
unnamed: IC4.3 (EN/SYNC), R4.2, R5.1
unnamed: IC4.1 (FB), R11.1
unnamed: IC4.8 (PG), R6.1
unnamed: C27.2, IC4.6 (SW), L2.1
unnamed: C25.1, IC4.2 (VCC), R6.2
unnamed: IC5.4 (BST), R14.1
unnamed: IC5.3 (EN/SYNC), R8.2
unnamed: IC5.1 (FB), R13.1
unnamed: C28.2, IC5.6 (SW), L3.1
unnamed: C26.1, IC5.2 (VCC), R7.2
unnamed: R11.2, R15.1, R17.1
unnamed: R13.2, R16.1, R18.1
unnamed: R9.2, R10.1, U2.5 (FB)
unnamed: L1.1, U2.3 (SW)
VCC: C18.1, C19.1, C20.1, C21.1, C22.1, C23.1, IC4.7 (IN), IC5.7 (IN), R4.1, R8.1, R19.1; also elsewhere on the board
VCC_Voltage: R19.2, R20.1; also elsewhere on the board

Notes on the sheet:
Vcc_Voltage=R2/(R1+R2)xVcc

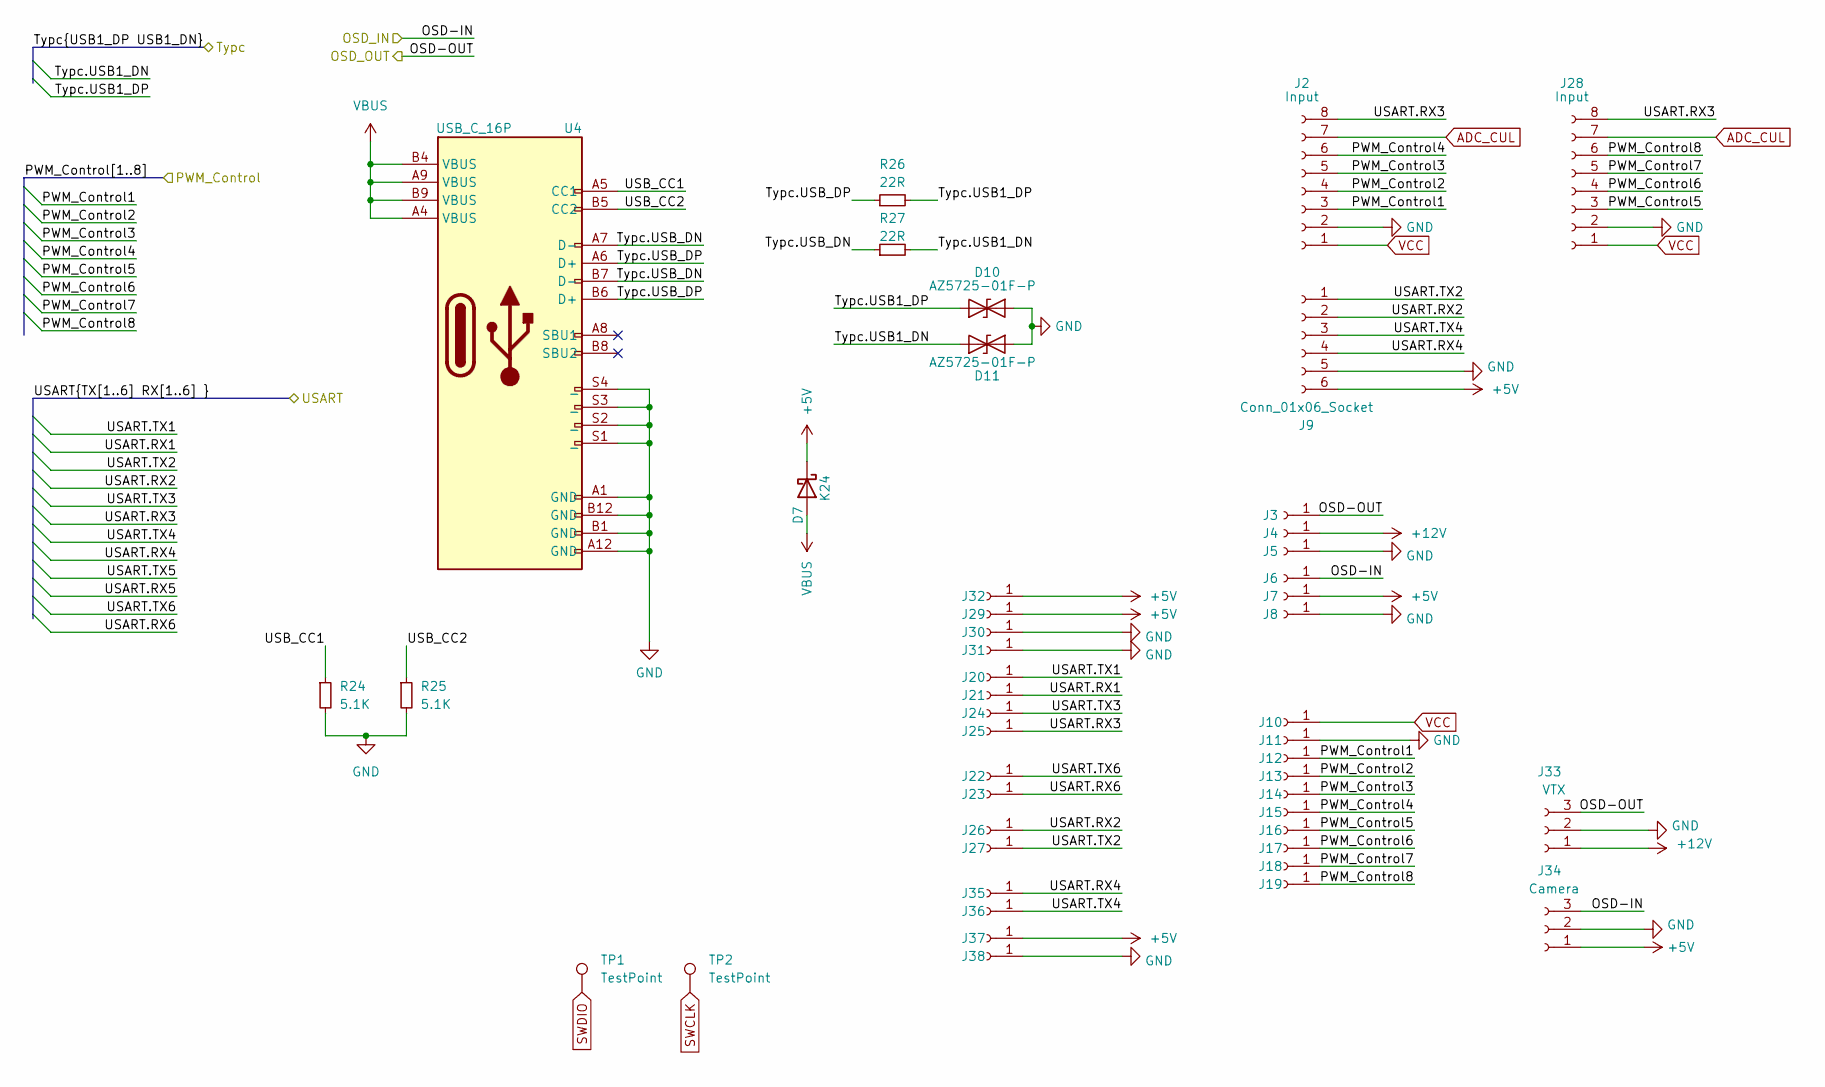
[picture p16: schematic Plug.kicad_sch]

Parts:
D7: K24; D_SOD-123F
D10, D11: AZ5725-01F-P; D_0402_1005Metric
J2, J28: Input; SH1.0mm_8P
J3, J4, J5, J6, J7, J8, J10, J11, J12, J13, J14, J15, J16, J17, J18, J19, J20, J21, J22, J23, J24, J25, J26, J27, J29, J30, J31, J32, J35, J36, J37, J38: Conn_01x01_Socket; Test
J9: Conn_01x06_Socket; JST_SM06B-SRSS-TB(LF)(SN)
J33: VTX; JST_SM03B-SRSS-TB(LF)(SN)
J34: Camera; JST_SM03B-SRSS-TB(LF)(SN)
R24, R25: 5.1K; R_0402_1005Metric
R26, R27: 22R; R_0402_1005Metric
TP1, TP2: TestPoint; Test
U4: USB_C_16P; Type-C 16P-SMD

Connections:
+5V: D7.1 (K), J7.1, J9.6, J29.1, J32.1, J34.1, J37.1; also elsewhere on the board
+12V: J4.1, J33.1; also elsewhere on the board
/PWM_Control1: J2.3, J12.1; also elsewhere on the board
/PWM_Control2: J2.4, J13.1; also elsewhere on the board
/PWM_Control3: J2.5, J14.1; also elsewhere on the board
/PWM_Control4: J2.6, J15.1; also elsewhere on the board
/PWM_Control5: J16.1, J28.3; also elsewhere on the board
/PWM_Control6: J17.1, J28.4; also elsewhere on the board
/PWM_Control7: J18.1, J28.5; also elsewhere on the board
/PWM_Control8: J19.1, J28.6; also elsewhere on the board
/Plug/OSD-IN: J6.1, J34.3; also elsewhere on the board
/Plug/OSD-OUT: J3.1, J33.3; also elsewhere on the board
/Plug/Typc.USB_DN: R27.1, U4.A7 (D-), U4.B7 (D-)
/Plug/Typc.USB_DP: R26.1, U4.A6 (D+), U4.B6 (D+)
/Plug/USB_CC1: R24.1, U4.A5 (CC1)
/Plug/USB_CC2: R25.1, U4.B5 (CC2)
/Typc.USB1_DN: D11.2 (A2), R27.2; also elsewhere on the board
/Typc.USB1_DP: D10.2 (A2), R26.2; also elsewhere on the board
/USART.RX1: J21.1; also elsewhere on the board
/USART.RX2: J9.2, J26.1; also elsewhere on the board
/USART.RX3: J2.8, J25.1, J28.8; also elsewhere on the board
/USART.RX4: J9.4, J35.1; also elsewhere on the board
/USART.RX6: J23.1; also elsewhere on the board
/USART.TX1: J20.1; also elsewhere on the board
/USART.TX2: J9.1, J27.1; also elsewhere on the board
/USART.TX3: J24.1; also elsewhere on the board
/USART.TX4: J9.3, J36.1; also elsewhere on the board
/USART.TX6: J22.1; also elsewhere on the board
ADC_CUL: J2.7, J28.7; also elsewhere on the board
GND: D10.1 (A1), D11.1 (A1), J2.2, J5.1, J8.1, J9.5, J11.1, J28.2, J30.1, J31.1, J33.2, J34.2, J38.1, R24.2, R25.2, U4.A1 (GND), U4.A12 (GND), U4.B1 (GND), U4.B12 (GND), U4.S1 (_), U4.S2 (_), U4.S3 (_), U4.S4 (_); also elsewhere on the board
SWCLK: TP2.1; also elsewhere on the board
SWDIO: TP1.1; also elsewhere on the board
VBUS: D7.2 (A), U4.A4 (VBUS), U4.A9 (VBUS), U4.B4 (VBUS), U4.B9 (VBUS)
VCC: J2.1, J10.1, J28.1; also elsewhere on the board

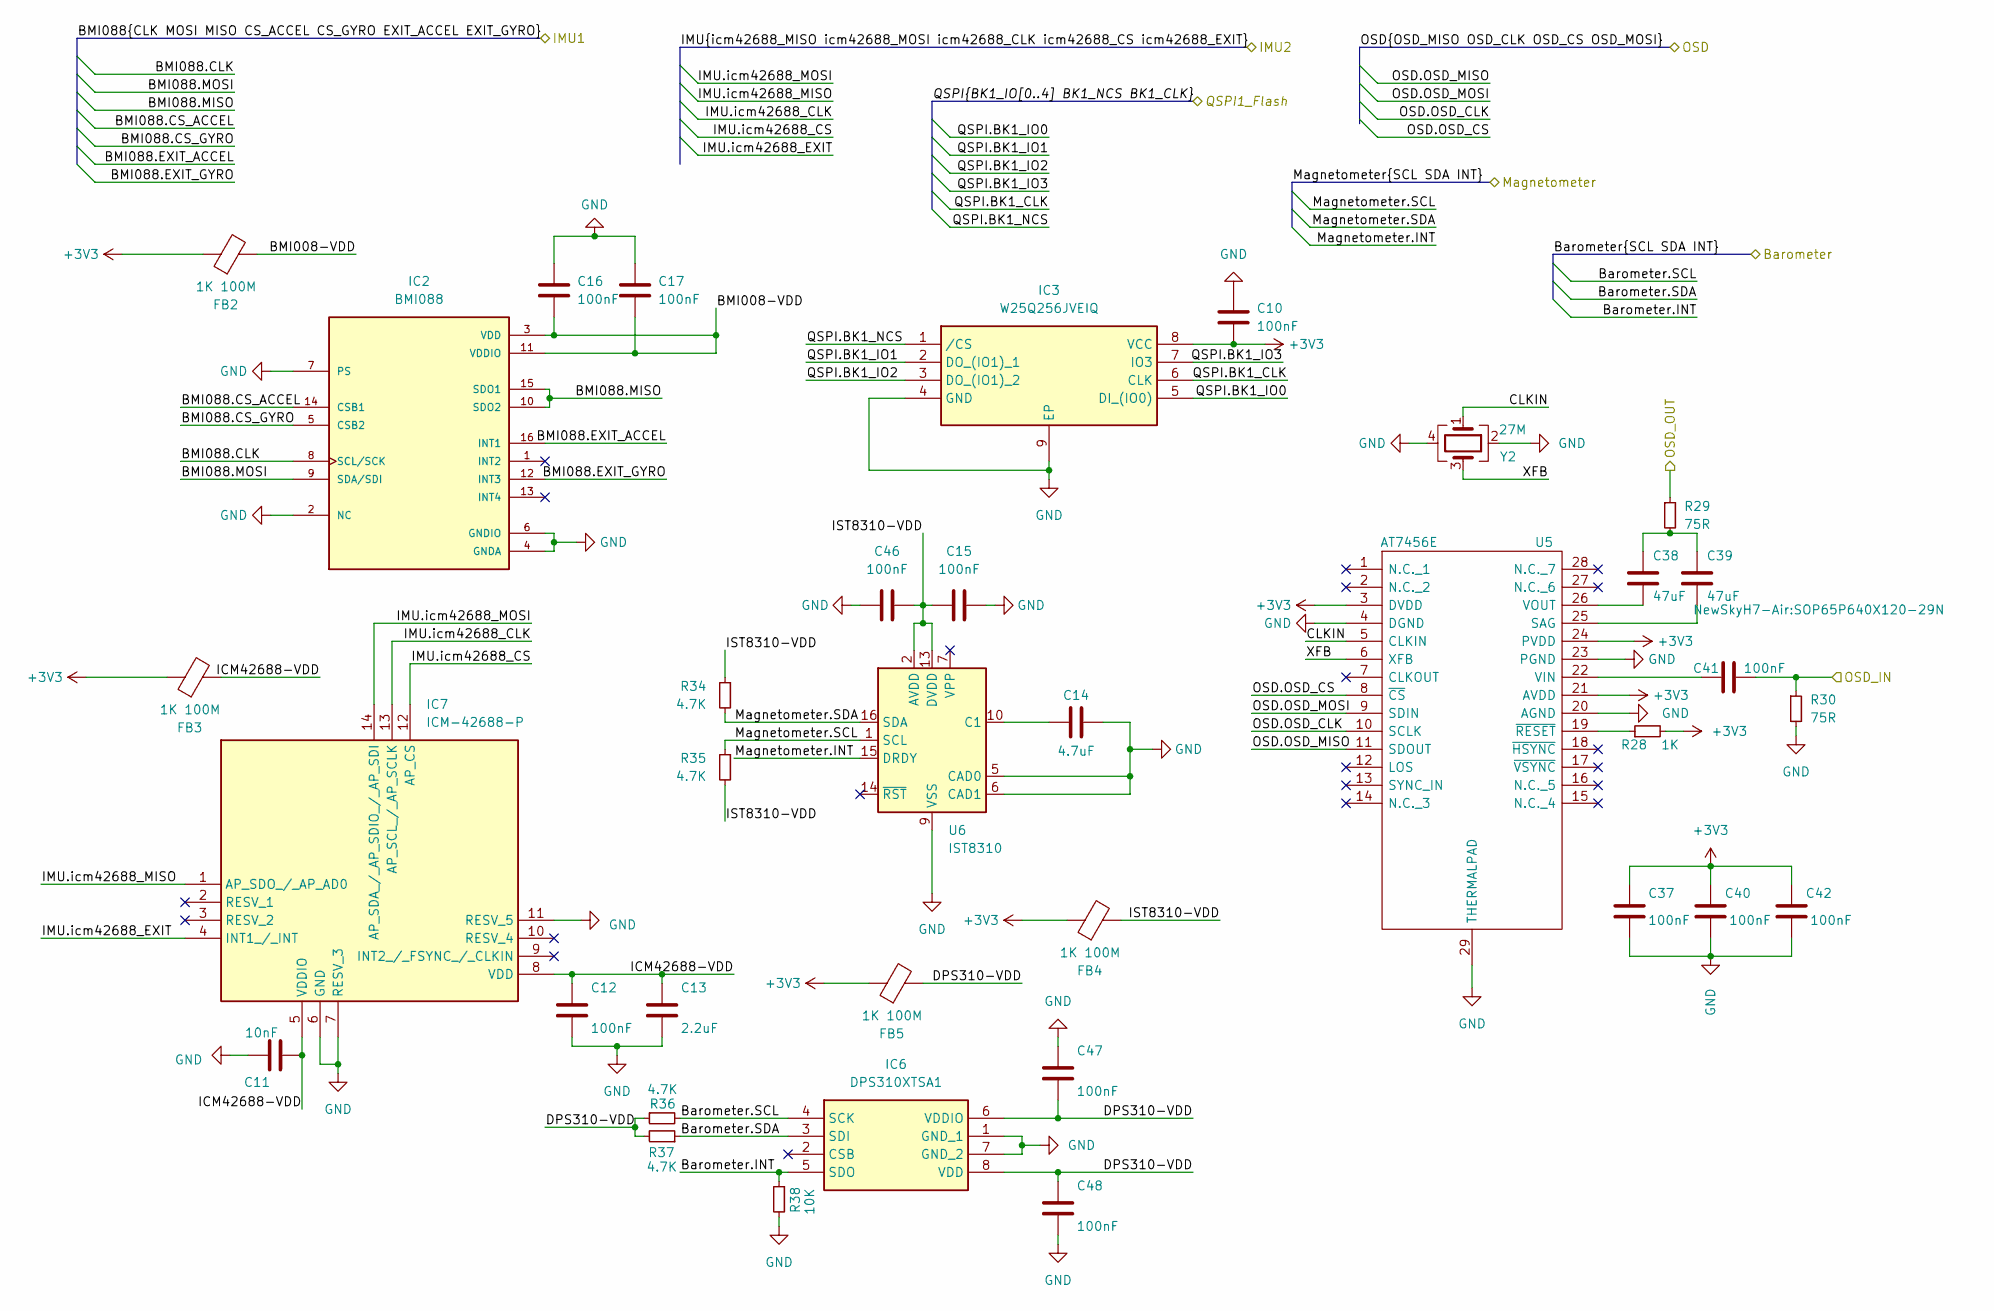
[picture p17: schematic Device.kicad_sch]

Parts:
C10, C12, C15, C16, C17, C37, C40, C41, C42, C46, C47, C48: 100nF; C_0402_1005Metric
C11: 10nF; C_0402_1005Metric
C13: 2.2uF; C_0402_1005Metric
C14: 4.7uF; C_0402_1005Metric
C38, C39: 47uF; C_0603_1608Metric
FB2, FB3, FB4, FB5: 1K 100M; L_0402_1005Metric
IC2: BMI088; PQFN50P450X300X100-16N
IC3: W25Q256JVEIQ; SON127P800X600X80-9N-D
IC6: DPS310XTSA1
IC7: ICM-42688-P; IIM42352; Manufacturer_Part_Number ICM-42688-P; Mouser Part Number 410-ICM-42688-P
R28: 1K; R_0402_1005Metric
R29, R30: 75R; R_0402_1005Metric
R34, R35, R36, R37: 4.7K; R_0402_1005Metric
R38: 10K; R_0402_1005Metric
U5: AT7456E; SOP65P640X120-29N; Manufacturer_Part_Number AT7456E
U6: IST8310; LGA-16_3x3mm_P0.5mm
Y2: 27M; Crystal_SMD_2016-4Pin_2.0x1.6mm

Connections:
+3V3: C10.2, C37.1, C40.1, C42.1, FB2.1, FB3.1, FB4.1, FB5.1, IC3.8 (VCC), R28.2, U5.3 (DVDD), U5.21 (AVDD), U5.24 (PVDD); also elsewhere on the board
/BMI088.CLK: IC2.8 (SCL/SCK); also elsewhere on the board
/BMI088.CS_ACCEL: IC2.14 (CSB1); also elsewhere on the board
/BMI088.CS_GYRO: IC2.5 (CSB2); also elsewhere on the board
/BMI088.EXIT_ACCEL: IC2.16 (INT1); also elsewhere on the board
/BMI088.EXIT_GYRO: IC2.12 (INT3); also elsewhere on the board
/BMI088.MISO: IC2.10 (SDO2), IC2.15 (SDO1); also elsewhere on the board
/BMI088.MOSI: IC2.9 (SDA/SDI); also elsewhere on the board
/Barometer.INT: IC6.5 (SDO), R38.1; also elsewhere on the board
/Barometer.SCL: IC6.4 (SCK), R36.2; also elsewhere on the board
/Barometer.SDA: IC6.3 (SDI), R37.1; also elsewhere on the board
/Device/BMI008-VDD: C16.1, C17.1, FB2.2, IC2.3 (VDD), IC2.11 (VDDIO)
/Device/CLKIN: U5.5 (CLKIN), Y2.1
/Device/DPS310-VDD: C47.2, C48.1, FB5.2, IC6.6 (VDDIO), IC6.8 (VDD), R36.1, R37.2
/Device/ICM42688-VDD: C11.2, C12.1, C13.1, FB3.2, IC7.5 (VDDIO), IC7.8 (VDD)
/Device/IST8310-VDD: C15.1, C46.2, FB4.2, R34.1, R35.2, U6.2 (AVDD), U6.13 (DVDD)
/Device/XFB: U5.6 (XFB), Y2.3
/IMU.icm42688_CLK: IC7.13 (AP_SCL_/_AP_SCLK); also elsewhere on the board
/IMU.icm42688_CS: IC7.12 (AP_CS); also elsewhere on the board
/IMU.icm42688_EXIT: IC7.4 (INT1_/_INT); also elsewhere on the board
/IMU.icm42688_MISO: IC7.1 (AP_SDO_/_AP_AD0); also elsewhere on the board
/IMU.icm42688_MOSI: IC7.14 (AP_SDA_/_AP_SDIO_/_AP_SDI); also elsewhere on the board
/Magnetometer.INT: U6.15 (DRDY); also elsewhere on the board
/Magnetometer.SCL: R35.1, U6.1 (SCL); also elsewhere on the board
/Magnetometer.SDA: R34.2, U6.16 (SDA); also elsewhere on the board
/OSD.OSD_CLK: U5.10 (SCLK); also elsewhere on the board
/OSD.OSD_CS: U5.8 (~CS); also elsewhere on the board
/OSD.OSD_MISO: U5.11 (SDOUT); also elsewhere on the board
/OSD.OSD_MOSI: U5.9 (SDIN); also elsewhere on the board
/Plug/OSD-IN: C41.2, R30.1; also elsewhere on the board
/Plug/OSD-OUT: R29.1; also elsewhere on the board
/QSPI.BK1_CLK: IC3.6 (CLK); also elsewhere on the board
/QSPI.BK1_IO0: IC3.5 (DI_(IO0)); also elsewhere on the board
/QSPI.BK1_IO1: IC3.2 (DO_(IO1)_1); also elsewhere on the board
/QSPI.BK1_IO2: IC3.3 (DO_(IO1)_2); also elsewhere on the board
/QSPI.BK1_IO3: IC3.7 (IO3); also elsewhere on the board
/QSPI.BK1_NCS: IC3.1 (/CS); also elsewhere on the board
GND: C10.1, C11.1, C12.2, C13.2, C14.1, C15.2, C16.2, C17.2, C37.2, C40.2, C42.2, C46.1, C47.1, C48.2, IC2.2 (NC), IC2.4 (GNDA), IC2.6 (GNDIO), IC2.7 (PS), IC3.4 (GND), IC3.9 (EP), IC6.1 (GND_1), IC6.7 (GND_2), IC7.6 (GND), IC7.7 (RESV_3), IC7.11 (RESV_5), R30.2, R38.2, U5.4 (DGND), U5.20 (AGND), U5.23 (PGND), U5.29 (THERMALPAD), U6.5 (CAD0), U6.6 (CAD1), U6.9 (VSS), U6.11 (VSS), Y2.2, Y2.4; also elsewhere on the board
unnamed: C38.1, C39.1, R29.2
unnamed: C39.2, U5.25 (SAG)
unnamed: C41.1, U5.22 (VIN)
unnamed: C38.2, U5.26 (VOUT)
unnamed: R28.1, U5.19 (~RESET)
unnamed: C14.2, U6.10 (C1)

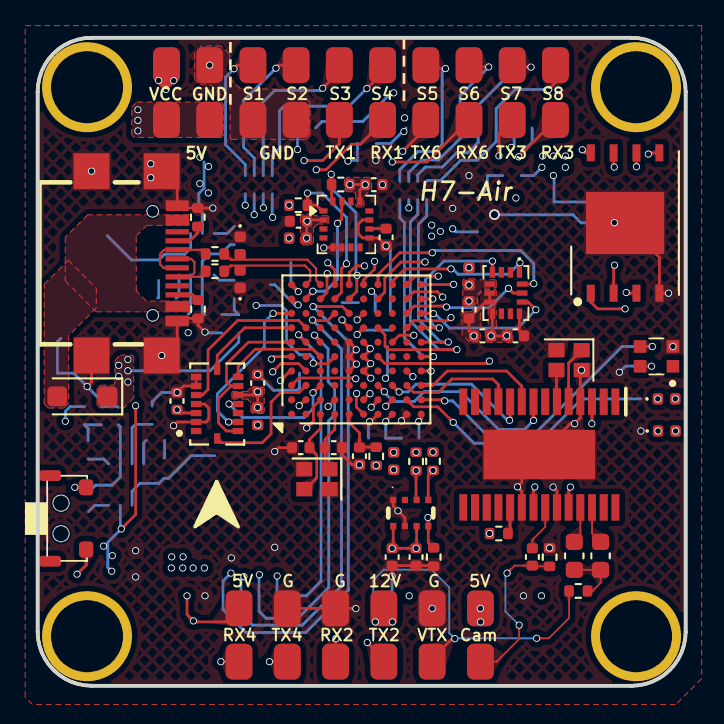
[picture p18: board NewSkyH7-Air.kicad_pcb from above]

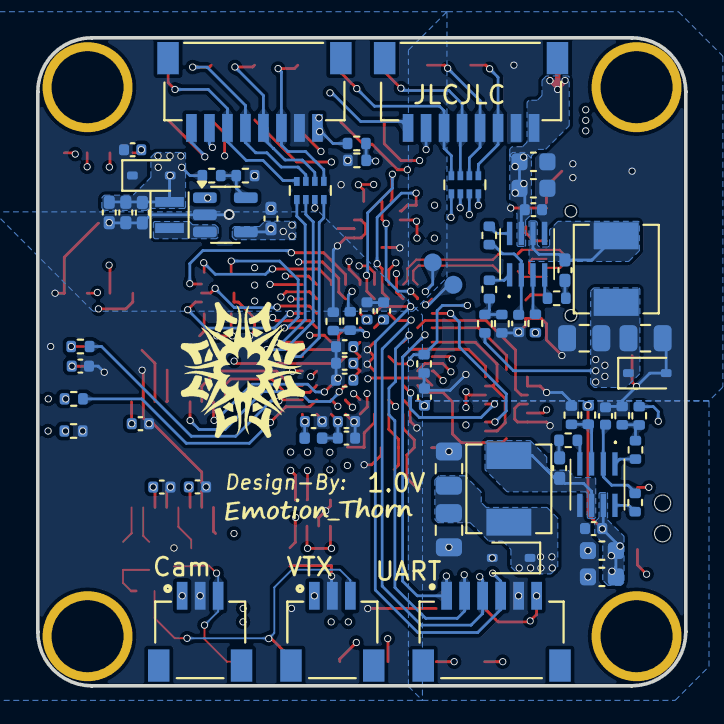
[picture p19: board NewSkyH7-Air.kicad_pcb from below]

Board: 6 copper layers, 36.0 x 36.0 mm, 157 parts (74 on the bottom side), 115 nets.

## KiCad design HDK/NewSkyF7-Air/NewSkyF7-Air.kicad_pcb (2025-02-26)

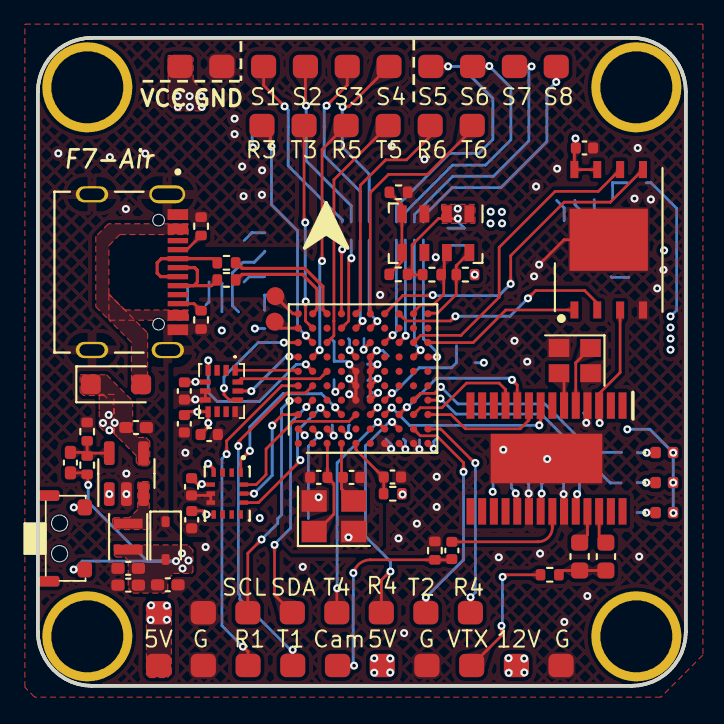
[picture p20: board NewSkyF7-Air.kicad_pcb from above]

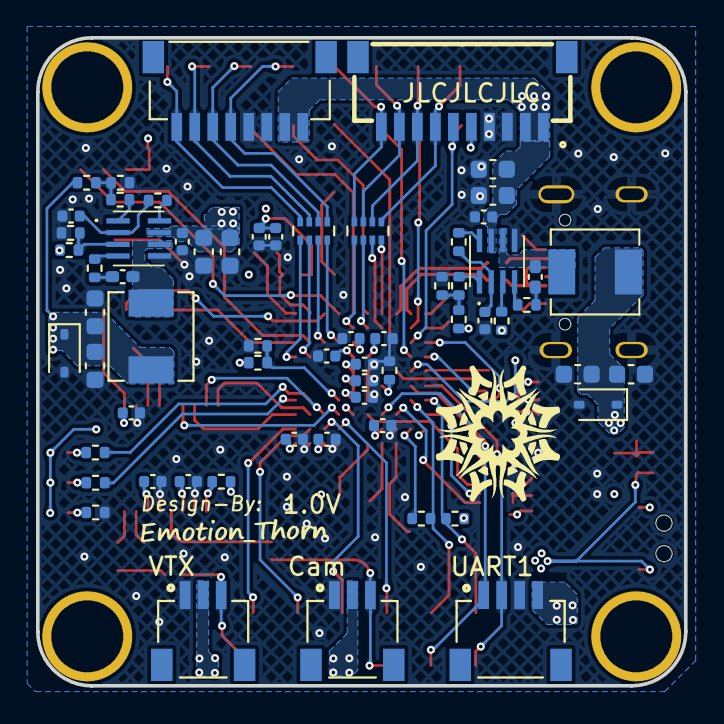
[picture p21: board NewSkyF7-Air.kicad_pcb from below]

Board: 4 copper layers, 36.0 x 36.0 mm, 147 parts (63 on the bottom side), 105 nets.

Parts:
C1, C2, C3, C4: 10uF; C_0603_1608Metric
C5, C6, C8, C9, C22, C24, C25, C27, C29, C30, C31, C32, C33, C36, C37, C38, C40, C41, C42, C44, C46: 100nF; C_0402_1005Metric
C7: 4.7uF; C_0402_1005Metric_Pad0.74x0.62mm_HandSolder
C10, C11: 100nF; C_0402_1005Metric_Pad0.74x0.62mm_HandSolder
C12: 6.8pF; C_0402_1005Metric_Pad0.74x0.62mm_HandSolder
C13, C16, C19: 10uF; C_0402_1005Metric_Pad0.74x0.62mm_HandSolder
C14, C15, C17, C18: 22uF; C_0603_1608Metric
C20, C21: 15pF; C_0402_1005Metric
C23: 4.7uF; C_0402_1005Metric
C26, C28, C45: 2.2uF; C_0402_1005Metric
C34, C35: 47uF; C_0603_1608Metric
C43: 10nF; C_0402_1005Metric
D1, D2, D3: LESD3Z5.0CMT1G; D_SOD-323
D4: Red; LED_0402_1005Metric
D5: Yellow; LED_0402_1005Metric
D6: Blue; LED_0402_1005Metric
D7: K24; D_SOD-123F
IC1, IC2: MP9943GQ-Z; MP9943GQZ
IC3: ICM-42688-P; IMC4288P
IC4: W25Q256JVEIQ; SON127P800X600X80-9N-D
J1: SBUS; JST_SM04B-SRSS-TB(LF)(SN)
J2: VTX; JST_SM03B-SRSS-TB(LF)(SN)
J3: Camera; JST_SM03B-SRSS-TB(LF)(SN)
J4: Input; SH1.0mm_8P
J5, J6, J7, J8, J9, J10, J11, J12, J13, J14, J15, J16, J17, J18, J19, J20, J21, J22, J23, J24, J25, J26, J27, J28, J29, J30, J31, J32, J33, J34, J37, J38, J39, J40: Conn_01x01_Socket; Test
J35: NewSkyF7
J36: Conn_01x10_Socket; SM10B-SRSS-TB
J41, J42: Conn_01x01_Socket; TestPoint_Pad_D1.0mm
L1: 2.2uH; L_Murata_DFE201610P
L2, L3: L; L_Sunlord_MWSA0402S
R1, R2, R3, R4, R6, R33: 100K; R_0402_1005Metric
R5: 442K; R_0402_1005Metric
R7, R9: 51K; R_0402_1005Metric
R8, R10, R24, R25: 22R; R_0402_1005Metric
R11: 3K; R_0402_1005Metric
R12: 7.68K; R_0402_1005Metric
R13, R14: 41.2K; R_0402_1005Metric
R15, R18, R19, R29, R30, R34, R35: 10K; R_0402_1005Metric
R16, R26: 1K; R_0402_1005Metric
R17: 3.3K; R_0402_1005Metric
R20, R21: 1k; R_0402_1005Metric
R22, R23: 5.1K; R_0402_1005Metric
R27, R28: 75R; R_0402_1005Metric
R31, R32: [N/S]; R_0402_1005Metric
RN1, RN2: 22R; R_Array_Concave_4x0402
SW1: BOOT0; 2x4_side
U1: TLV62569DBV; SOT-23-5
U2: STM32F745VGH6; TFBGA-100_8x8mm_Layout10x10_P0.8mm
U4: USB_C_16P; Typc-C-16P
U5: AT7456E; SOP65P640X120-29N
U6: BMI270; XDCR_BMI270
U8: MS5611-01BA; LGA-8_3x5mm_P1.25mm
Y1: 25M; Crystal_SMD_3225-4Pin_3.2x2.5mm
Y2: 27M; Crystal_SMD_2520-4Pin_2.5x2.0mm

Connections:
+3V3: C12.1, C13.1, C16.1, C19.1, C23.1, C24.1, C25.1, C27.1, C29.1, C30.1, C31.1, C32.2, C33.1, C36.1, C38.1, C40.1, C41.1, C42.2, C43.2, C44.1, C45.1, C46.2, D3.2 (A2), D4.2 (A), D5.2 (A), D6.2 (A), IC3.5 (VDDIO), IC3.8 (VDD), IC4.3 (DO_(IO1)_2), IC4.7 (IO3), IC4.8 (VCC), L1.2, R5.1, R19.1, R26.2, R29.1, R30.2, R32.1, R34.1, R35.2, SW1.1, U2.B2 (VBAT), U2.D2 (VDD), U2.F4 (VDD), U2.F5 (VDD), U2.F6 (VDDUSB), U2.F7 (PDE_ON), U2.H1 (VDDA), U2.K1 (VDD), U5.3 (DVDD), U5.21 (AVDD), U5.24 (PVDD), U6.5 (VDDIO), U6.8 (VDD), U8.1 (VDD), U8.2 (PS)
+5V: C7.1, C15.2, C18.2, D2.1 (A1), D7.1 (K), J1.4, J3.2, J10.1, J20.1, J29.1, L3.2, R14.2, U1.1 (EN), U1.4 (VIN)
+12V: C14.2, C17.2, D1.1 (A1), J2.2, J19.1, L2.2, R13.2
/Devices/AT7456/CLKIN: U5.5 (CLKIN), Y2.1
/Devices/AT7456/XFB: U5.6 (XFB), Y2.3
/Devices/BOOT0: R18.1, SW1.2, U2.D5 (BOOT0)
/Devices/IMU.BMI270_CLK: U2.A3 (PE2), U6.13 (SCX)
/Devices/IMU.BMI270_CS: U2.C3 (PE4), U6.12 (CSB)
/Devices/IMU.BMI270_EXIT: U2.A2 (PC13), U6.4 (INT1)
/Devices/IMU.BMI270_MISO: U2.D3 (PE5), U6.1 (SDO)
/Devices/IMU.BMI270_MOSI: U2.E3 (PE6), U6.14 (SDX)
/Devices/IMU.icm42688_CLK: IC3.13 (AP_SCL_/_AP_SCLK), U2.A7 (PB3)
/Devices/IMU.icm42688_CS: IC3.12 (AP_CS), U2.A8 (PA15)
/Devices/IMU.icm42688_EXIT: IC3.4 (INT1_/_INT), U2.B6 (PD5)
/Devices/IMU.icm42688_MISO: IC3.1 (AP_SDO_/_AP_AD0), U2.A6 (PB4)
/Devices/IMU.icm42688_MOSI: IC3.14 (AP_SDA_/_AP_SDIO_/_AP_SDI), U2.C6 (PD6)
/Devices/NRST: C22.1, R19.2, U2.E1 (NRST)
/Devices/OSC_IN: C20.1, U2.D1 (PH0-OSC_IN), Y1.3
/Devices/OSC_OUT: C21.1, U2.C1 (PH1-OSC_OUT), Y1.1
/Devices/OSD.OSD_CLK: U2.H3 (PA5), U5.10 (SCLK)
/Devices/OSD.OSD_CS: U2.G3 (PA4), U5.8 (~CS)
/Devices/OSD.OSD_MISO: U2.J3 (PA6), U5.11 (SDOUT)
/Devices/OSD.OSD_MOSI: U2.K3 (PA7), U5.9 (SDIN)
/Devices/PA8: RN1.3 (R3.1), U2.D9 (PA8)
/Devices/PA10: RN1.4 (R4.1), U2.D10 (PA10)
/Devices/PA13: J42.1, U2.A10 (PA13)
/Devices/PA14: J41.1, U2.A9 (PA14)
/Devices/PB0: R20.2, U2.J4 (PB0)
/Devices/PB1: R21.2, U2.K4 (PB1)
/Devices/PB10: RN2.6 (R3.2), U2.J7 (PB10)
/Devices/PB11: RN2.5 (R4.2), U2.K7 (PB11)
/Devices/PC8: RN1.1 (R1.1), U2.F9 (PC8)
/Devices/PC9: RN1.2 (R2.1), U2.E9 (PC9)
/Devices/PD14: RN2.7 (R2.2), U2.H8 (PD14)
/Devices/PD15: RN2.8 (R1.2), U2.G8 (PD15)
/Devices/PWM_Control1: J14.1, J36.7, RN1.5 (R4.2)
/Devices/PWM_Control2: J13.1, J36.8, RN1.6 (R3.2)
/Devices/PWM_Control3: J12.1, J36.9, RN1.7 (R2.2)
/Devices/PWM_Control4: J11.1, J36.10, RN1.8 (R1.2)
/Devices/PWM_Control5: J4.5, J18.1, RN2.1 (R1.1)
/Devices/PWM_Control6: J4.6, J17.1, RN2.2 (R2.1)
/Devices/PWM_Control7: J4.7, J16.1, RN2.3 (R3.1)
/Devices/PWM_Control8: J4.8, J15.1, RN2.4 (R4.1)
/Devices/Plugs/OSD-IN: C37.2, J3.3, J28.1, R28.1
/Devices/Plugs/OSD-OUT: J2.3, J27.1, R27.1
/Devices/Plugs/Typc.USB_DN: R25.1, U4.A7 (D-), U4.B7 (D-)
/Devices/Plugs/Typc.USB_DP: R24.1, U4.A6 (D+), U4.B6 (D+)
/Devices/Plugs/USB_CC1: R22.1, U4.A5 (CC1)
/Devices/Plugs/USB_CC2: R23.1, U4.B5 (CC2)
/Devices/Pressure_Sensor.MS5611_CLK: R30.1, U2.K10 (PD12), U8.8 (SCLK)
/Devices/Pressure_Sensor.MS5611_SDA: R29.2, U2.J10 (PD13), U8.7 (SDI/SDA)
/Devices/SPI2.Flash_CLK: IC4.6 (CLK), U2.J8 (PB13)
/Devices/SPI2.Flash_CS: IC4.1 (/CS), U2.K8 (PB12)
/Devices/SPI2.Flash_MISO: IC4.2 (DO_(IO1)_1), U2.H10 (PB14)
/Devices/SPI2.Flash_MOSI: IC4.5 (DI_(IO0)), U2.G10 (PB15)
/Devices/Typc.USB1_DN: R25.2, U2.C10 (PA11)
/Devices/Typc.USB1_DP: R24.2, U2.B10 (PA12)
/Devices/USART.RX1: J1.2, J23.1, U2.A5 (PB7)
/Devices/USART.RX2: J40.1, U2.K2 (PA3)
/Devices/USART.RX3: J36.6, J38.1, U2.B8 (PC11)
/Devices/USART.RX4: J26.1, U2.H2 (PA1)
/Devices/USART.RX5: J8.1, U2.B7 (PD2)
/Devices/USART.RX6: J6.1, U2.E10 (PC7)
/Devices/USART.TX1: J1.1, J24.1, U2.B5 (PB6)
/Devices/USART.TX2: J39.1, U2.J2 (PA2)
/Devices/USART.TX3: J37.1, U2.B9 (PC10)
/Devices/USART.TX4: J25.1, U2.G2 (PA0)
/Devices/USART.TX5: J7.1, U2.C8 (PC12)
/Devices/USART.TX6: J5.1, U2.F10 (PC6)
ADC_CUL: J36.5, U2.F3 (PC3)
GND: C1.2, C2.2, C3.2, C4.2, C5.2, C6.2, C7.2, C8.2, C9.2, C13.2, C14.1, C15.1, C16.2, C17.1, C18.1, C19.2, C20.2, C21.2, C22.2, C23.2, C24.2, C25.2, C26.2, C27.2, C28.2, C29.2, C30.2, C31.2, C32.1, C33.2, C36.2, C38.2, C40.2, C41.2, C42.1, C43.1, C44.2, C45.2, C46.1, D1.2 (A2), D2.2 (A2), D3.1 (A1), IC1.5 (GND), IC2.5 (GND), IC3.6 (GND), IC3.7 (RESV_3), IC3.11 (RESV_5), IC4.4 (GND), IC4.9 (EP), J1.3, J2.1, J3.1, J4.3, J4.4, J9.1, J21.1, J22.1, J30.1, J33.1, J36.3, J36.4, R6.2, R11.2, R12.2, R16.2, R17.2, R18.2, R22.2, R23.2, R28.2, R31.2, R33.2, U1.2 (GND), U2.C2 (VSS), U2.E4 (VSS), U2.E5 (VSS), U2.E6 (BYPASS_REG), U2.G1 (VSSA), U2.J1 (VSS), U4.A1 (GND), U4.A12 (GND), U4.B1 (GND), U4.B12 (GND), U4.S1 (_), U4.S2 (_), U4.S3 (_), U4.S4 (_), U5.4 (DGND), U5.20 (AGND), U5.23 (PGND), U5.29 (THERMALPAD), U6.6 (GNDIO), U6.7 (GND), U8.3 (GND), Y1.2, Y1.4, Y2.2, Y2.4
I2C1.SCL: J32.1, R35.1, U2.B4 (PB8)
I2C1.SDA: J31.1, R34.2, U2.A4 (PB9)
unnamed: C10.1, R8.2
unnamed: C11.1, R10.2
unnamed: C34.1, C35.1, R27.2
unnamed: D4.1 (K), R17.1
unnamed: D5.1 (K), R20.1
unnamed: D6.1 (K), R21.1
unnamed: IC1.4 (BST), R8.1
unnamed: IC1.3 (EN/SYNC), R2.2, R33.1
unnamed: IC1.1 (FB), R7.1
unnamed: IC1.8 (PG), R1.1
unnamed: C10.2, IC1.6 (SW), L2.1
unnamed: C8.1, IC1.2 (VCC), R1.2
unnamed: IC2.4 (BST), R10.1
unnamed: IC2.3 (EN/SYNC), R4.2
unnamed: IC2.1 (FB), R9.1
unnamed: IC2.8 (PG), R3.1
unnamed: C11.2, IC2.6 (SW), L3.1
unnamed: C9.1, IC2.2 (VCC), R3.2
unnamed: R7.2, R11.1, R13.1
unnamed: R9.2, R12.1, R14.1
unnamed: R31.1, R32.2, U8.4 (CSB), U8.5 (CSB)
unnamed: C12.2, R5.2, R6.1, U1.5 (FB)
unnamed: L1.1, U1.3 (SW)
unnamed: C26.1, U2.F8 (VCAP_1)
unnamed: C28.1, U2.E7 (VCAP_2)
unnamed: C35.2, U5.25 (SAG)
unnamed: C37.1, U5.22 (VIN)
unnamed: C34.2, U5.26 (VOUT)
unnamed: R26.1, U5.19 (~RESET)
VBUS: D7.2 (A), U4.A4 (VBUS), U4.A9 (VBUS), U4.B4 (VBUS), U4.B9 (VBUS)
VCC: C1.1, C2.1, C3.1, C4.1, C5.1, C6.1, IC1.7 (IN), IC2.7 (IN), J4.1, J4.2, J34.1, J36.1, J36.2, R2.1, R4.1, R15.1
VCC_Voltage: R15.2, R16.1, U2.G4 (PC4)

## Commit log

2023-10-13 Add Control-F4
    [Control-F4.kicad_pcb, Control-F4.kicad_sch]
2023-12-01 Add HDK
    [Control-F4.kicad_pcb, Control-F4.kicad_sch]
2023-12-01 Add make doc
    [bom.csv, designators.csv, positions.csv]
2023-12-07 Add NewSkyF7-Air Hardware design Kit
    [Devices.kicad_sch, Flash.kicad_sch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]
2025-02-26 Add about NewSky 3D files
    [DPS310XTSA1.stp]
2025-02-26 Add NewSky kicad symbol library
2025-02-26 Add NewSky kicad package library
2025-02-26 Upadte NewSky kicad symbol library
2025-02-26 Add NewSkyH7-Air (use STM32H743 size:36x36mm)
    [DC-DC.kicad_sch, Device.kicad_sch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]
